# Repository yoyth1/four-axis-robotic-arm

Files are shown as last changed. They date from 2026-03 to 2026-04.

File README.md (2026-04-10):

# Four-Axis Robotic Arm (STM32 + Unity + MATLAB)

本项目为四轴机械臂毕业设计开源仓库，包含机械结构设计、运动学建模验证、硬件电路设计以及 STM32 驱动与上位机联动。

## 项目概览

- 机械结构：基于 SolidWorks 建模，完成底座、腰关节、大臂、小臂与夹爪结构设计。
- 运动学：完成正运动学与逆运动学推导，并用 MATLAB 进行验证。
- 硬件设计：包含控制板/电路相关资料与 PCB 源文件。
- 控制系统：下位机使用 STM32（Keil 工程），上位机使用 Unity 3D。

## 效果与资料预览

### 结构图与样机实物

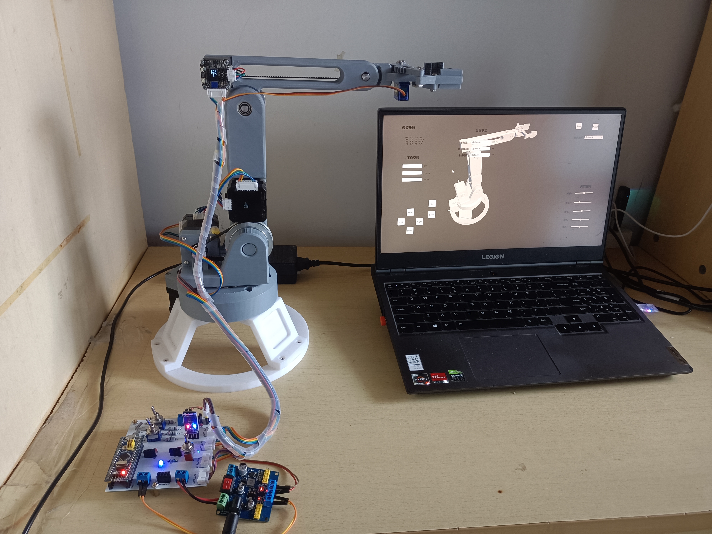
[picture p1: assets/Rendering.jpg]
Rendering

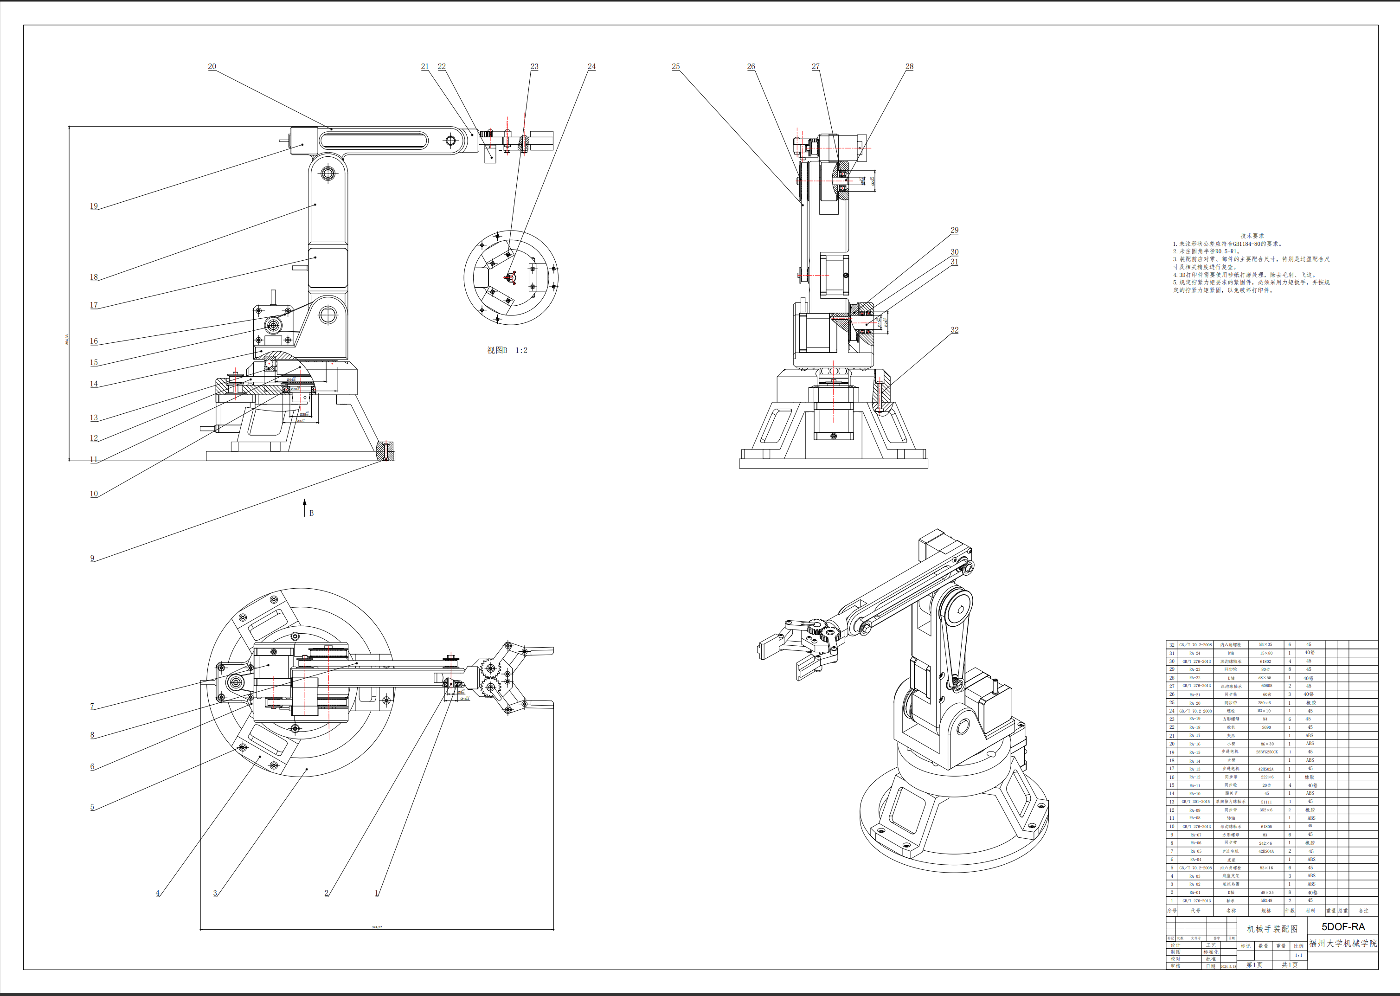
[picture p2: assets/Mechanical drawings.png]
Mechanical drawings.png

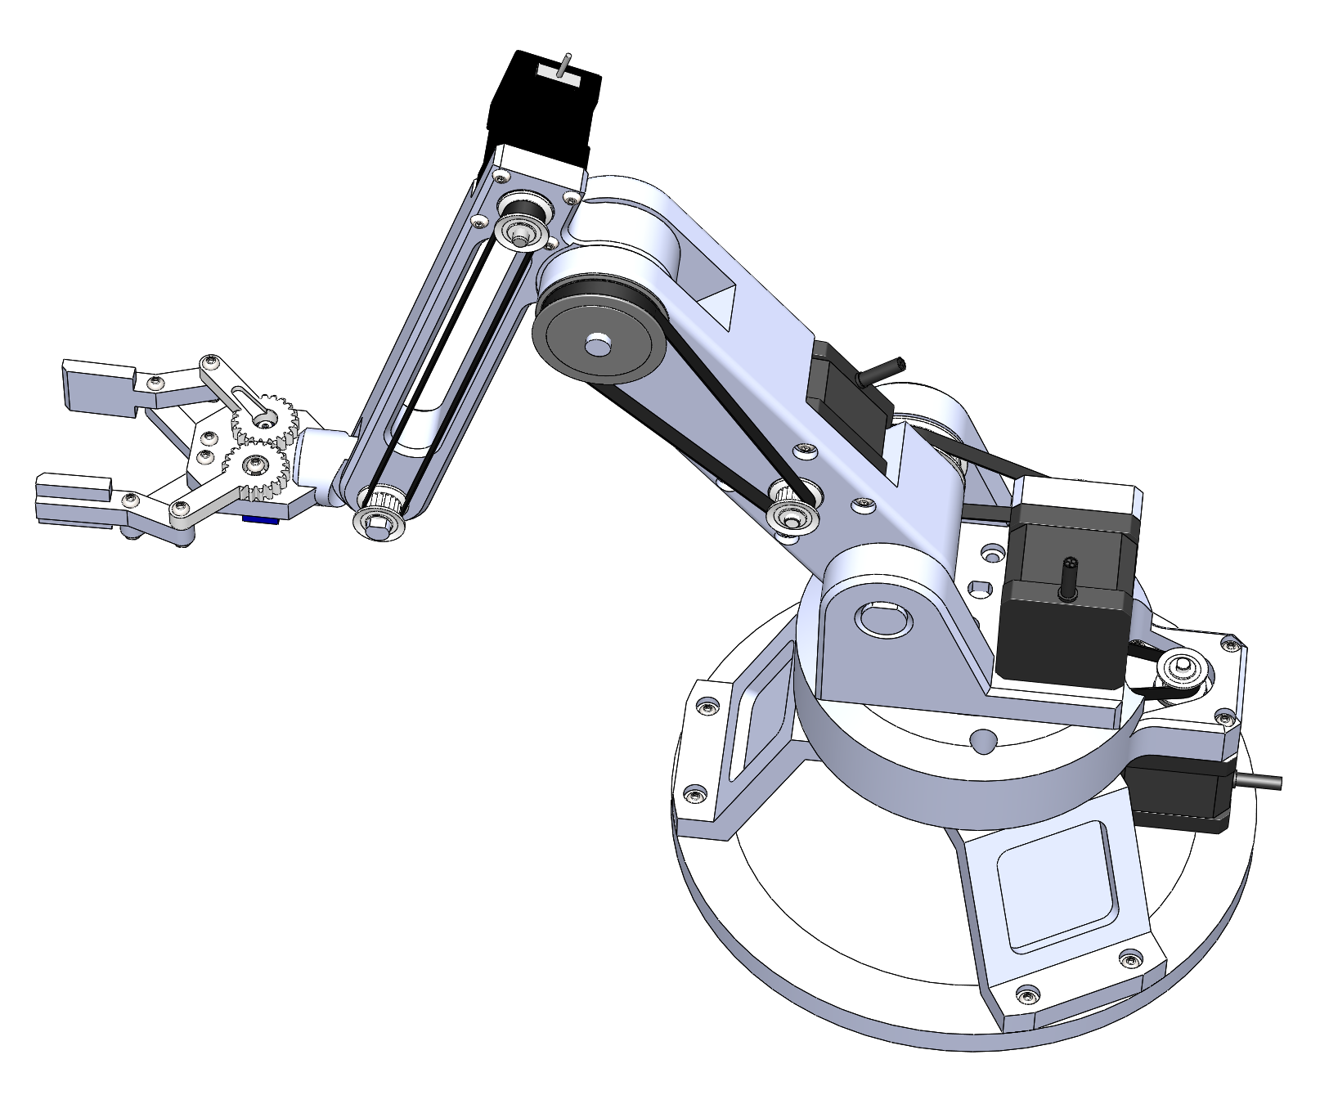
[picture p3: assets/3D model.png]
3D Model


### 系统电路

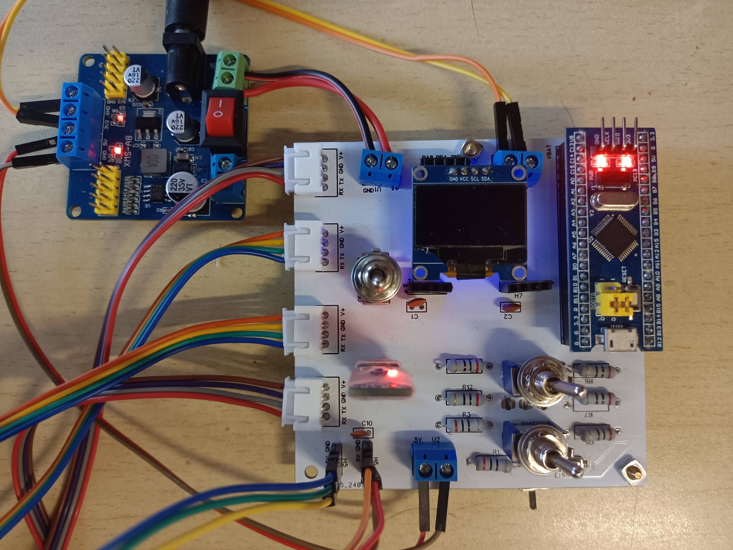
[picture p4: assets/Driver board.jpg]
Driver Board

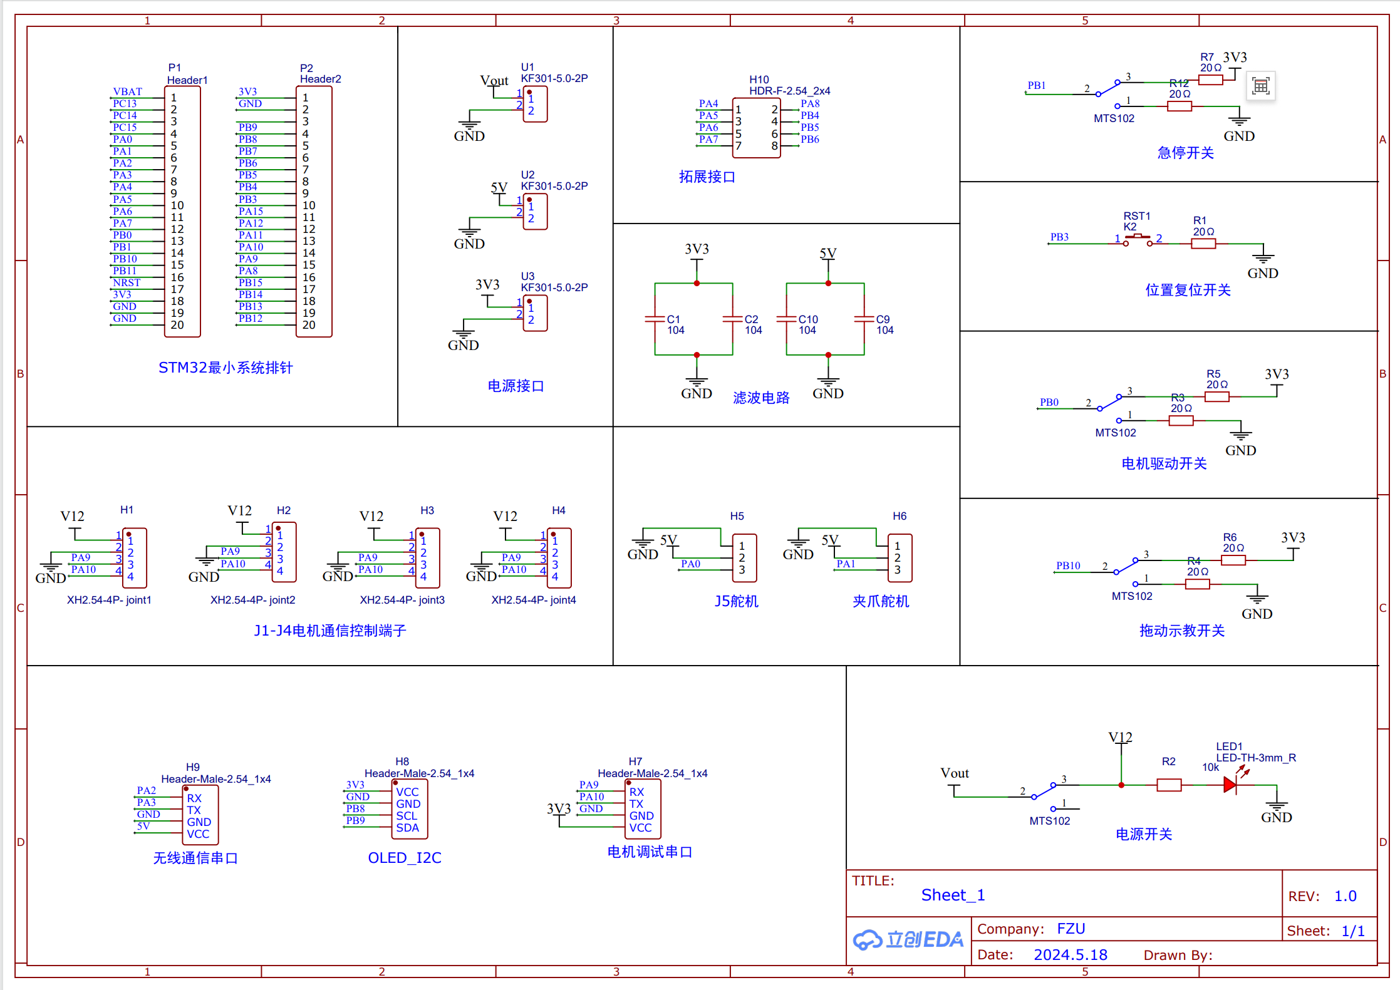
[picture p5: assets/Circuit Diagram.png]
Circuit Diagram


### 上位机界面

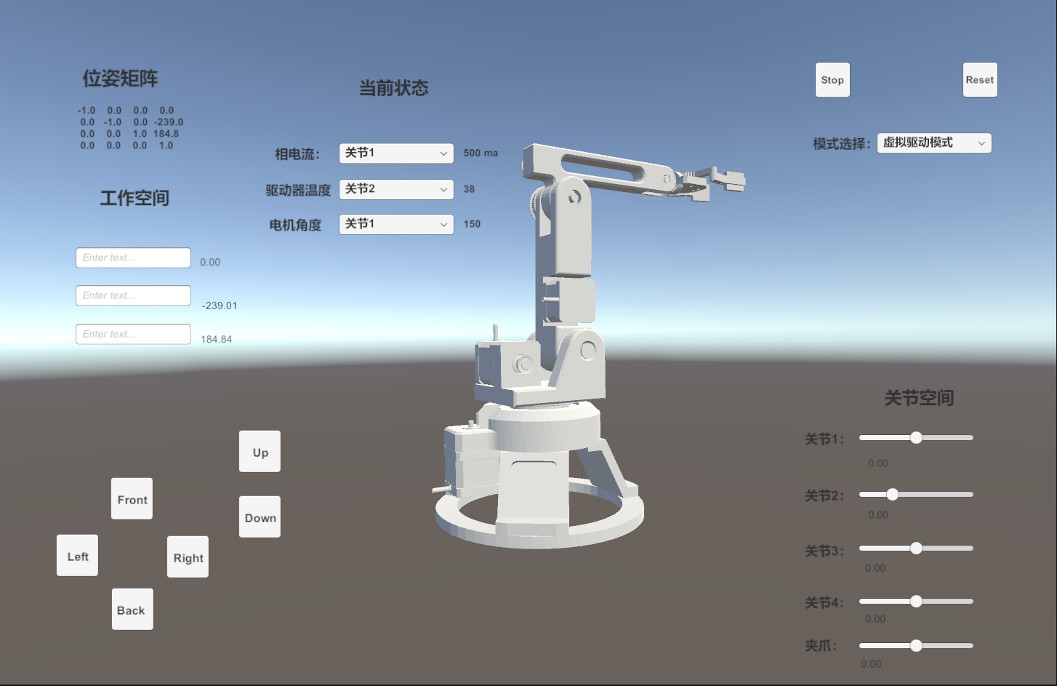
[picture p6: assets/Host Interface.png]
Host Interface


## 仓库结构

| 路径 | 说明 |
|---|---|
| `app/` | Unity 3D 上位机程序（当前仓库为构建产物） |
| `matlab/` | 运动学验证代码（含 D-H 建模与逆解相关脚本） |
| `model/` | 机械臂 3D 模型Solidworks文件 |
| `assets/` | README 图片、电路图、机械图纸等资料 |
| `Stm32_Project/` | STM32 下位机控制代码（Keil 工程） |

## DH 参数与正逆运动学

机械臂采用标准 D-H 建模，共 5 个连杆（4 个主控关节 + 末端夹爪）。MATLAB 验证代码见 `matlab/dh.m` 与 `matlab/inverse_kinematics.m`。

### D-H 参数表

| 连杆 | $\theta$ | $d$ (mm) | $a$ (mm) | $\alpha$ (°) |
|:---:|:---:|:---:|:---:|:---:|
| 0-1 | $-90°+\theta_1$ | 0 | 29 | -90 |
| 1-2 | $-90°+\theta_2$ | 0 | 150 | 0 |
| 2-3 | $75°+\theta_3$ | 0 | 134.5 | 0 |
| 3-4 | $65°+\theta_4$ | 0 | 0 | 90 |
| 4-5 | $-90°+\theta_5$ | 80 | 0 | 90 |

### 正运动学

将各关节 D-H 变换矩阵依次右乘，得到末端相对基座的总变换矩阵：

$$
A_1 =
\begin{bmatrix}
C_1 & 0 & -S_1 & a_1 C_1 \\
S_1 & 0 & C_1 & a_1 S_1 \\
0 & -1 & 0 & 0 \\
0 & 0 & 0 & 1
\end{bmatrix}
$$

$$
A_2 =
\begin{bmatrix}
C_2 & -S_2 & 0 & a_2 C_2 \\
S_2 & C_2 & 0 & a_2 S_2 \\
0 & 0 & 1 & 0 \\
0 & 0 & 0 & 1
\end{bmatrix}
$$

$$
A_3 =
\begin{bmatrix}
C_3 & -S_3 & 0 & a_3 C_3 \\
S_3 & C_3 & 0 & a_3 S_3 \\
0 & 0 & 1 & 0 \\
0 & 0 & 0 & 1
\end{bmatrix}
$$

$$
A_4 =
\begin{bmatrix}
C_4 & 0 & S_4 & 0 \\
S_4 & 0 & -C_4 & 0 \\
0 & 1 & 0 & 0 \\
0 & 0 & 0 & 1
\end{bmatrix}
$$

$$
A_5 =
\begin{bmatrix}
C_5 & 0 & S_5 & 0 \\
S_5 & 0 & -C_5 & 0 \\
0 & 1 & 0 & d_5 \\
0 & 0 & 0 & 1
\end{bmatrix}
$$

总变换矩阵展开式：

$$
{}^0T_H =
\begin{bmatrix}
C_{234}C_1C_5 - S_1S_5 & S_{234}C_1 & C_1 C_{234}S_5 + S_1C_5 & C_1(a_1 + d_5 S_{234} + a_3 C_{23} + a_2 C_2) \\
C_1S_5 + S_{234}S_1C_5 & S_{234}S_1 & S_1 C_{234}S_5 - C_1C_5 & S_1(a_1 + d_5 S_{234} + a_3 C_{23} + a_2 C_2) \\
-S_{234}C_5 & C_{234} & -S_{234}S_5 & d_5 C_{234} + a_3 S_{23} - a_2 S_2 \\
0 & 0 & 0 & 1
\end{bmatrix}
$$

### 逆运动学

为了方便表示，将上面的矩阵表示为 *RHS*（Right-Hand Side）。将机械臂末端的期望位姿表示为：

$$
{}^R T_H =
\begin{bmatrix}
n_x & o_x & a_x & p_x \\
n_y & o_y & a_y & p_y \\
n_z & o_z & a_z & p_z \\
0 & 0 & 0 & 1
\end{bmatrix}
$$

根据期望末端位姿 ${}^RT_H$，采用代数解耦法，依次反解各关节角，求解顺序如下：

**① 求 $\theta_5$**：由总变换矩阵 $(3,2)$ 元素对应关系得

$$
\theta_5 = \arctan\left(\frac{a_z}{n_z}\right)
$$

**② 求 $\theta_1$**：由 $(1,4)$、$(2,4)$ 元素得

$$
\theta_1 = \arctan\left(\frac{p_y - d_5 o_y}{p_x - d_5 o_x}\right)
$$

**③ 求 $\theta_3$**：利用 $\theta_1$ 已知，由 $(2,4)$、$(3,4)$ 建立方程后两边平方相加，利用 $S_2 S_{23} + C_2 C_{23} = C_3$ 化简得

$$
C_3 =
\frac{
\left(d_5 o_z - p_z\right)^2 +
\left(\dfrac{p_y - d_5 o_y}{S_1} - a_1\right)^2 -
a_2^2 - a_3^2
}{
2 a_2 a_3
}
$$

$$
\theta_3 =
\arctan\left(\frac{\pm\sqrt{1-C_3^2}}{C_3}\right)
$$

**④ 求 $\theta_2$**：令 $\tan\phi = \dfrac{a_3 S_3}{a_3 C_3 + a_2}$，则

$$
\theta_2 =
\arcsin\left(
\frac{d_5 o_z - p_z}{\sqrt{a_2^2 + a_3^2 + 2 a_2 a_3 C_3}}
\right) - \phi
$$

**⑤ 求 $\theta_4$**：由 $(3,3)$ 元素 $\cos(\theta_2+\theta_3+\theta_4) = o_z$ 得

$$
\theta_4 = \arccos(o_z) - \theta_2 - \theta_3
$$

## 环境与使用说明

### 1) STM32 下位机

- 工程路径：`Stm32_Project/Project.uvprojx`
- 目标芯片：`STM32F103C8`（Cortex-M3）
- 开发环境：Keil MDK（uVision）
- 使用方式：打开工程、编译后通过 ST-Link 等方式下载到开发板。
- 通过串口与上位机通信

### 2) MATLAB 运动学验证

- 代码路径：`matlab/`
- 主要脚本：`dh.m`、`inverse_kinematics.m`、`dof_5.m`
- 说明：脚本使用机器人运动学工具箱相关能力（如 `SerialLink`），需要配置matlab Robotic Toolbox工具箱。

### 3) Unity 上位机

- 程序路径：`app/`
- 说明：当前仓库目前仅提供上位机构建结果，可直接运行并与下位机联调。
  
### 演示视频
- https://www.bilibili.com/video/BV1QucRzZEsu/?vd_source=743b9fd8168666d94b81cdd6a7604898#reply116205826345706

## 开源说明

### License

 MIT 或其软硬件项目的许可证
### 免责声明

本项目主要用于学习与毕业设计交流。请在实际制作、调试和使用过程中自行评估风险，作者不对由此产生的直接或间接损失负责。

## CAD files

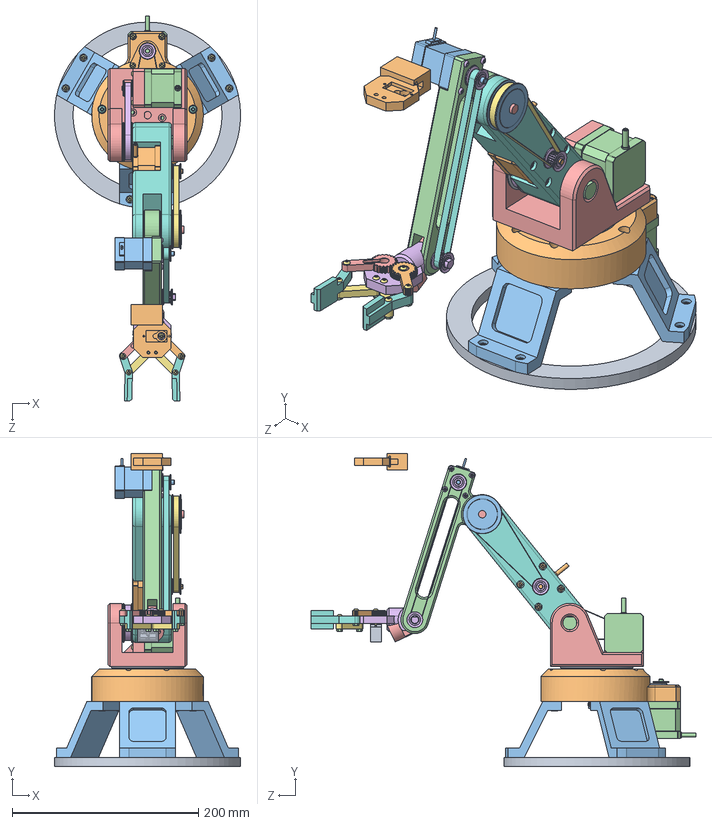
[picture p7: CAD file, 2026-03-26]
model/装配图.SLDASM
199.9 x 336.6 x 413.8 mm
底座环
底座盘
底座支架 x 3
42系列两相混合式步进电机[42HS04A] x 2
关节1
2GT型A形圆孔同步带轮[TPAC20GT2060-A-H4] x 5
GB╱T 276-2013[深沟球轴承[60000]61802] x 4
大臂
2GT型A形圆孔同步带轮[TPAC60GT2060-A-H8]
42系列两相混合式步进电机[42HS02A]
两相28系列混合式步进电机[28BYG250CK-SASSML-0071]
小臂
夹爪架
夹爪臂 x 2
夹爪小爪 x 2
A形树脂直齿轮[SGPOS1-20-10-A-8]
Servo Motor (SG90)(used)
齿轮2
直孔同步带轮 2GT型[60-2GT-6-6F] x 2
D轴15mm
d轴 x 2
D轴8x20
轴承8x14x4 x 2
GB╱T 276-2013[两面带防尘盖的深沟球轴承[60000-2Z]608-2Z] x 2
GB╱T 276-1994[两面带密封圈（接触式）的深沟球轴承[60000-2LS]61805-2LS]
GB╱T 70.2-2015[内六角平圆头螺钉M3×8] x 4
轴
轴盖
hexagon socket button head screws gb x 4
GB╱T 70.2-2015[内六角平圆头螺钉M3×16] x 21
GB╱T 70.2-2015[内六角平圆头螺钉M4×30] x 6
GB╱T 301-2015[单向推力球轴承[51000型]51111]
GB╱T 39-1988[方螺母 C级M3] x 6
GB╱T 39-1988[方螺母 C级M4] x 6
GB╱T 6170-2000[1型六角螺母 A级和B级M3] x 6
GB╱T 70.2-2008[内六角平圆头螺钉M3×10] x 3
同步带2^底座
同步带3^底座
零件3^底座
同步带1^底座

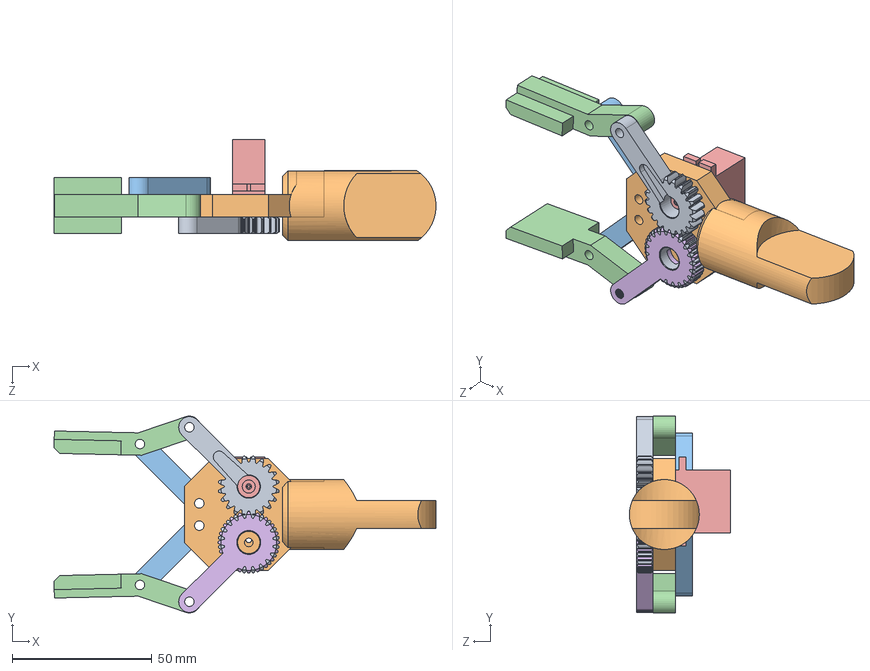
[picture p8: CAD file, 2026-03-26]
model/夹爪.SLDASM
136.6 x 70.4 x 36.2 mm
夹爪架
夹爪臂 x 2
夹爪小爪 x 2
A形树脂直齿轮[SGPOS1-20-10-A-8]
Servo Motor (SG90)(used)
齿轮2

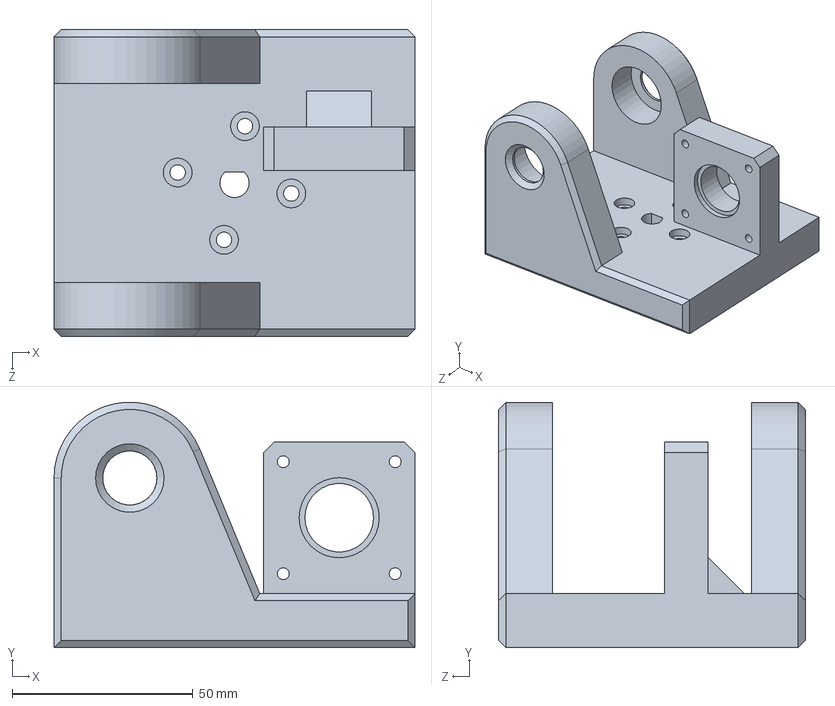
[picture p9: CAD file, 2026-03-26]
model/关节1.SLDPRT
100.0 x 68.0 x 85.0 mm

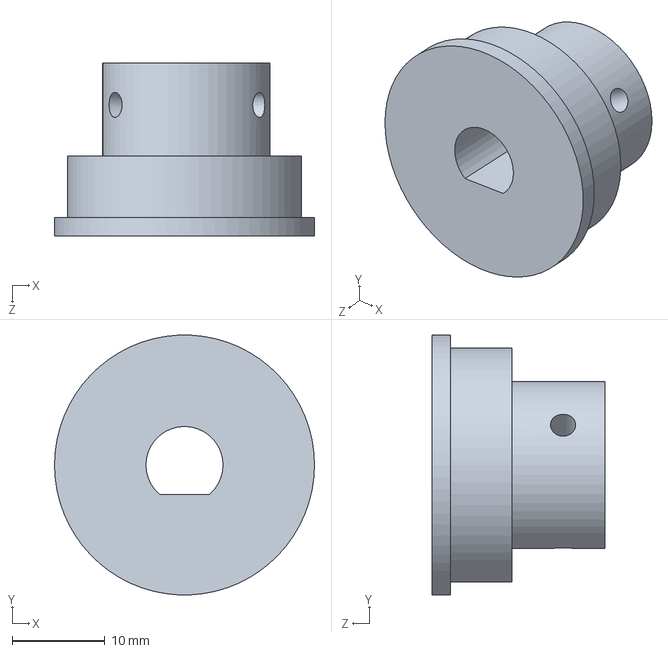
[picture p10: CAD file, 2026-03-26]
model/轴.SLDPRT
28.0 x 28.0 x 18.6 mm

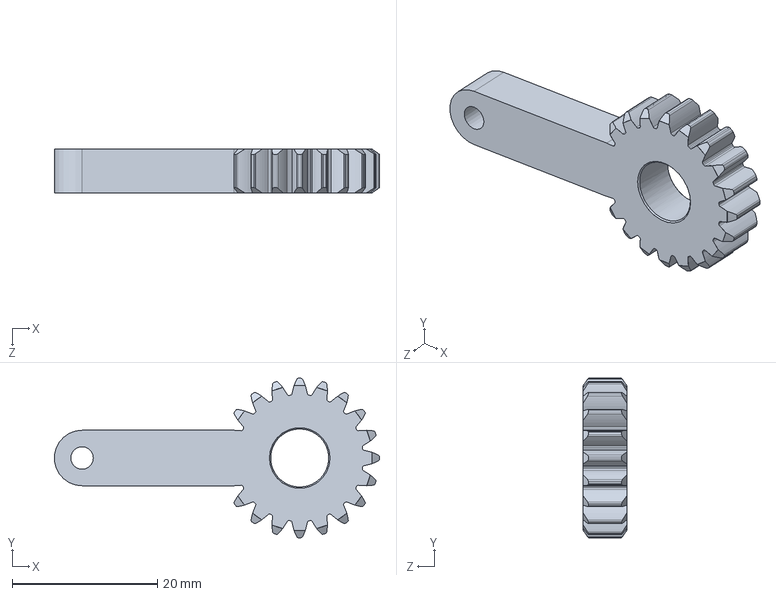
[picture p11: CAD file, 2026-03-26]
model/A形树脂直齿轮[SGPOS1-20-10-A-8].sldprt
44.8 x 22.0 x 6.00 mm

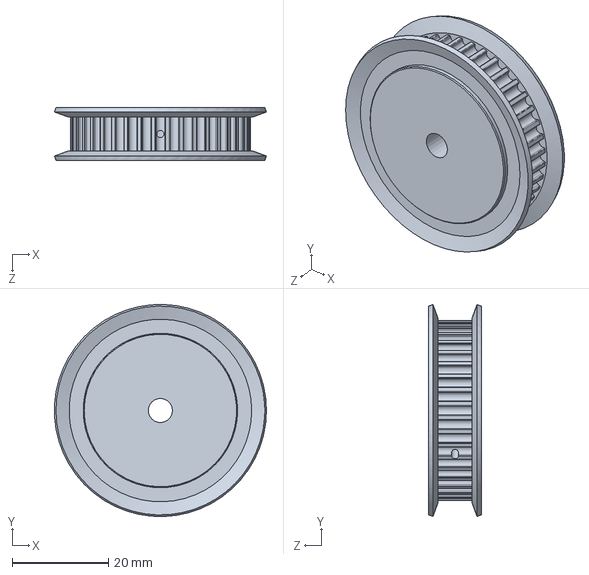
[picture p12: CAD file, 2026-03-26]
model/标准型圆弧型齿HTD3M-A同步轮支持定制[SLA40-3M060-A-P10].sldprt
44.0 x 44.0 x 11.0 mm

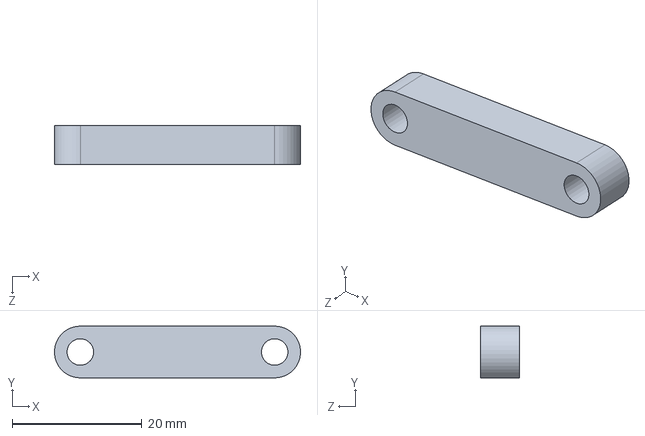
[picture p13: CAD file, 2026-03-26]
model/夹爪臂.SLDPRT
38.0 x 8.00 x 6.00 mm

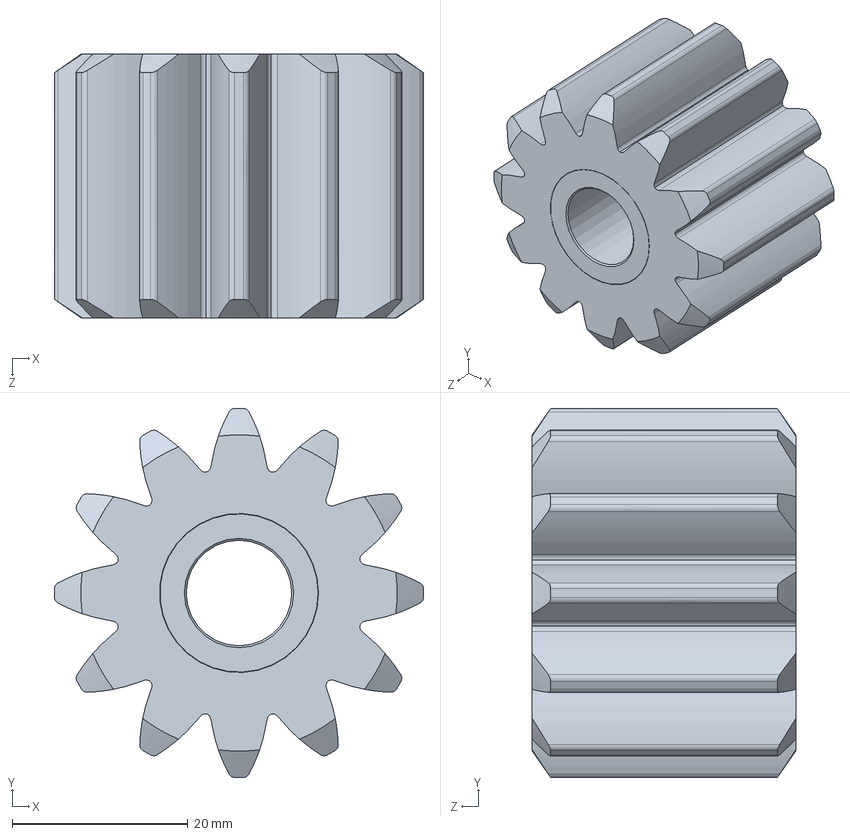
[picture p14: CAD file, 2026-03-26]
model/A形树脂直齿轮[SGMC3-12-30-A-12].sldprt
42.0 x 42.0 x 30.0 mm

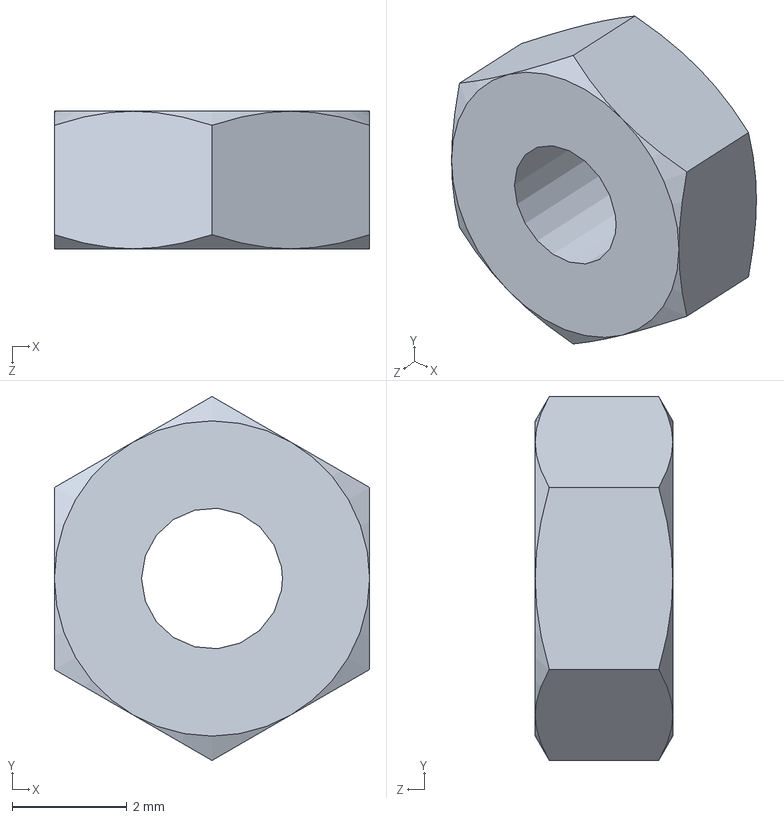
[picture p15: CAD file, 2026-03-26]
model/GB╱T 6170-2000[1型六角螺母 A级和B级M3].sldprt
5.50 x 6.35 x 2.40 mm

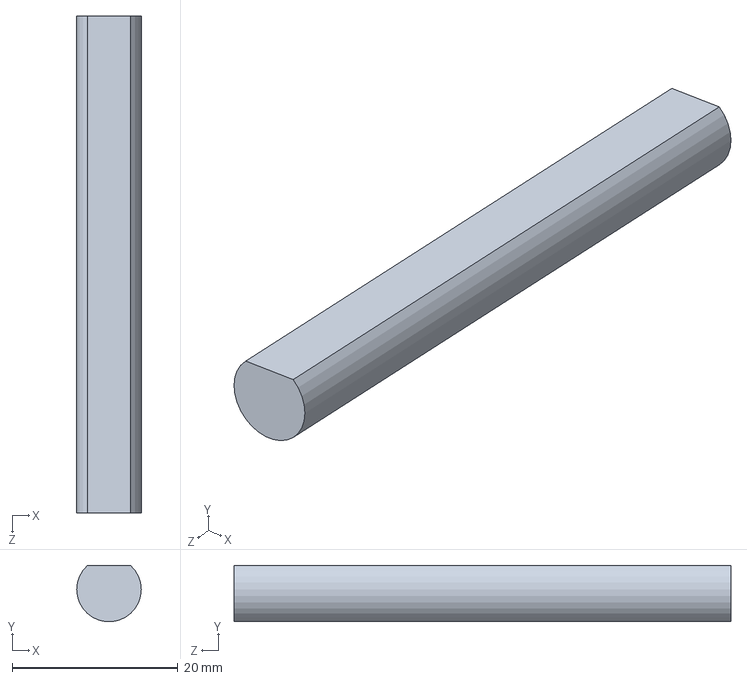
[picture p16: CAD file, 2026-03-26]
model/D轴8x20.SLDPRT
7.80 x 6.78 x 60.0 mm

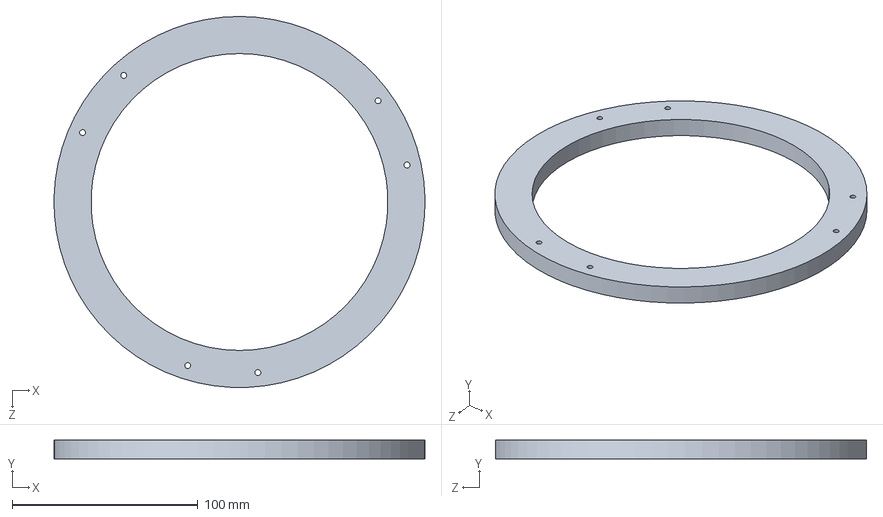
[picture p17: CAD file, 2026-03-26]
model/底座环.SLDPRT
199.9 x 10.0 x 200.0 mm

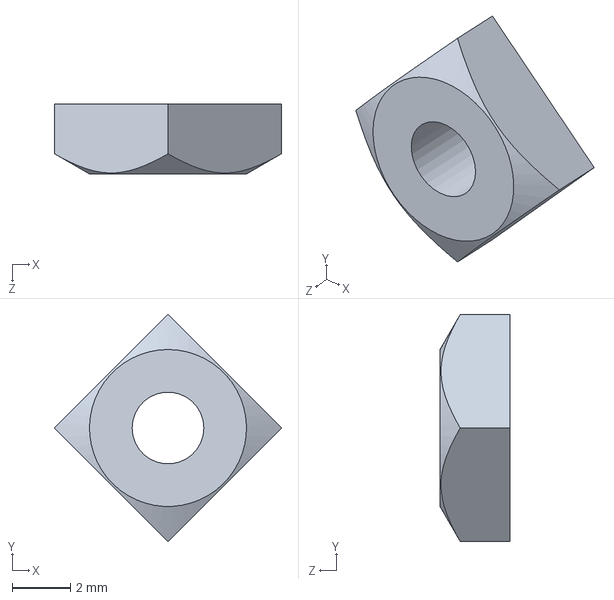
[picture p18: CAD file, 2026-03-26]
model/GB╱T 39-1988[方螺母 C级M3].sldprt
7.78 x 7.78 x 2.40 mm

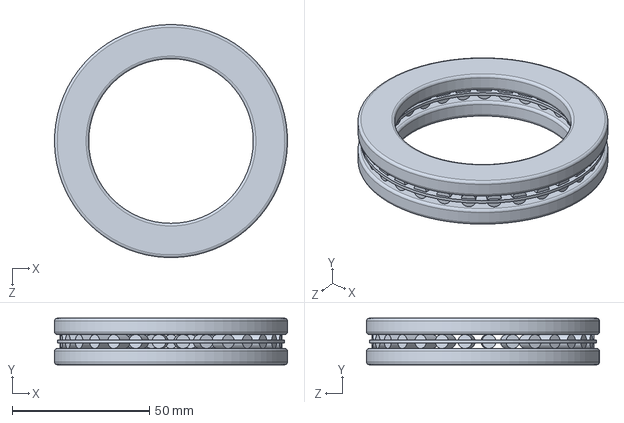
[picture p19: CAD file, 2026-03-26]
model/GB╱T 4663-2017[单向推力圆柱滚子轴承81112 GB╱T 4663-2017].sldprt
85.0 x 17.0 x 85.0 mm

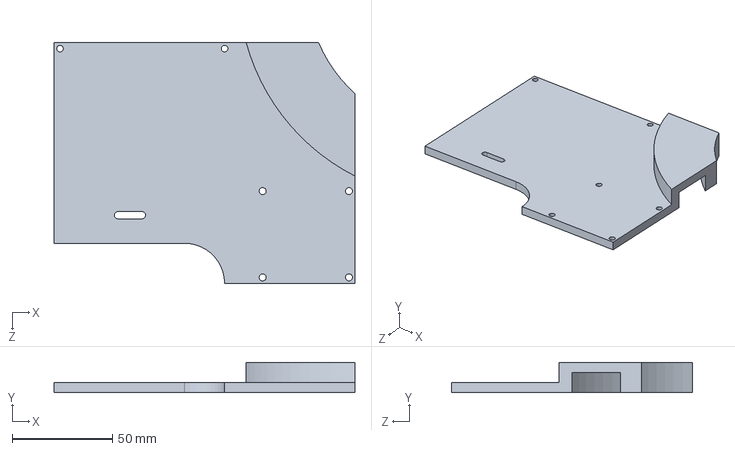
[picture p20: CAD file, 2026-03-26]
model/电路板支架.SLDPRT
150.0 x 15.0 x 120.0 mm

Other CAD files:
model/GB╱T 70.2-2015[内六角平圆头螺钉M3×8].sldprt
model/底座支架.SLDPRT
model/两相28系列混合式步进电机[28BYG250CK-SASSML-0071].SLDPRT
model/底座盘.SLDPRT
model/2GT型A形圆孔同步带轮[TPAC20GT2060-A-H4].sldprt
model/2GT型A形圆孔同步带轮[TPAC60GT2060-A-H8].sldprt
model/42系列两相混合式步进电机[42HS02A].sldprt
model/42系列两相混合式步进电机[42HS04A].sldprt
model/42系列两相混合式步进电机[42HS07A].sldprt
model/A形树脂直齿轮[SGMC3-14-30-A-12].sldprt
model/A形树脂直齿轮[SGPOS1.5-15-15-A-8].sldprt
model/A形树脂直齿轮[SGPOS2-14-20-A-10].sldprt
model/D轴15mm.SLDPRT
model/GB╱T 276-1994[两面带密封圈（接触式）的深沟球轴承[60000-2LS]61805-2LS].sldprt
model/GB╱T 276-2013[两面带防尘盖的深沟球轴承[60000-2Z]608-2Z].sldprt
model/GB╱T 276-2013[深沟球轴承[60000]61802].sldprt
model/GB╱T 301-2015[单向推力球轴承[51000型]51111].sldprt
model/GB╱T 39-1988[方螺母 C级M4].sldprt
model/GB╱T 4663-1994[推力圆柱滚子轴承[80000]81108].sldprt
model/GB╱T 4663-2017[单向推力圆柱滚子轴承81111 GB╱T 4663-2017].sldprt
model/GB╱T 70.2-2008[内六角平圆头螺钉M3×10].sldprt
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

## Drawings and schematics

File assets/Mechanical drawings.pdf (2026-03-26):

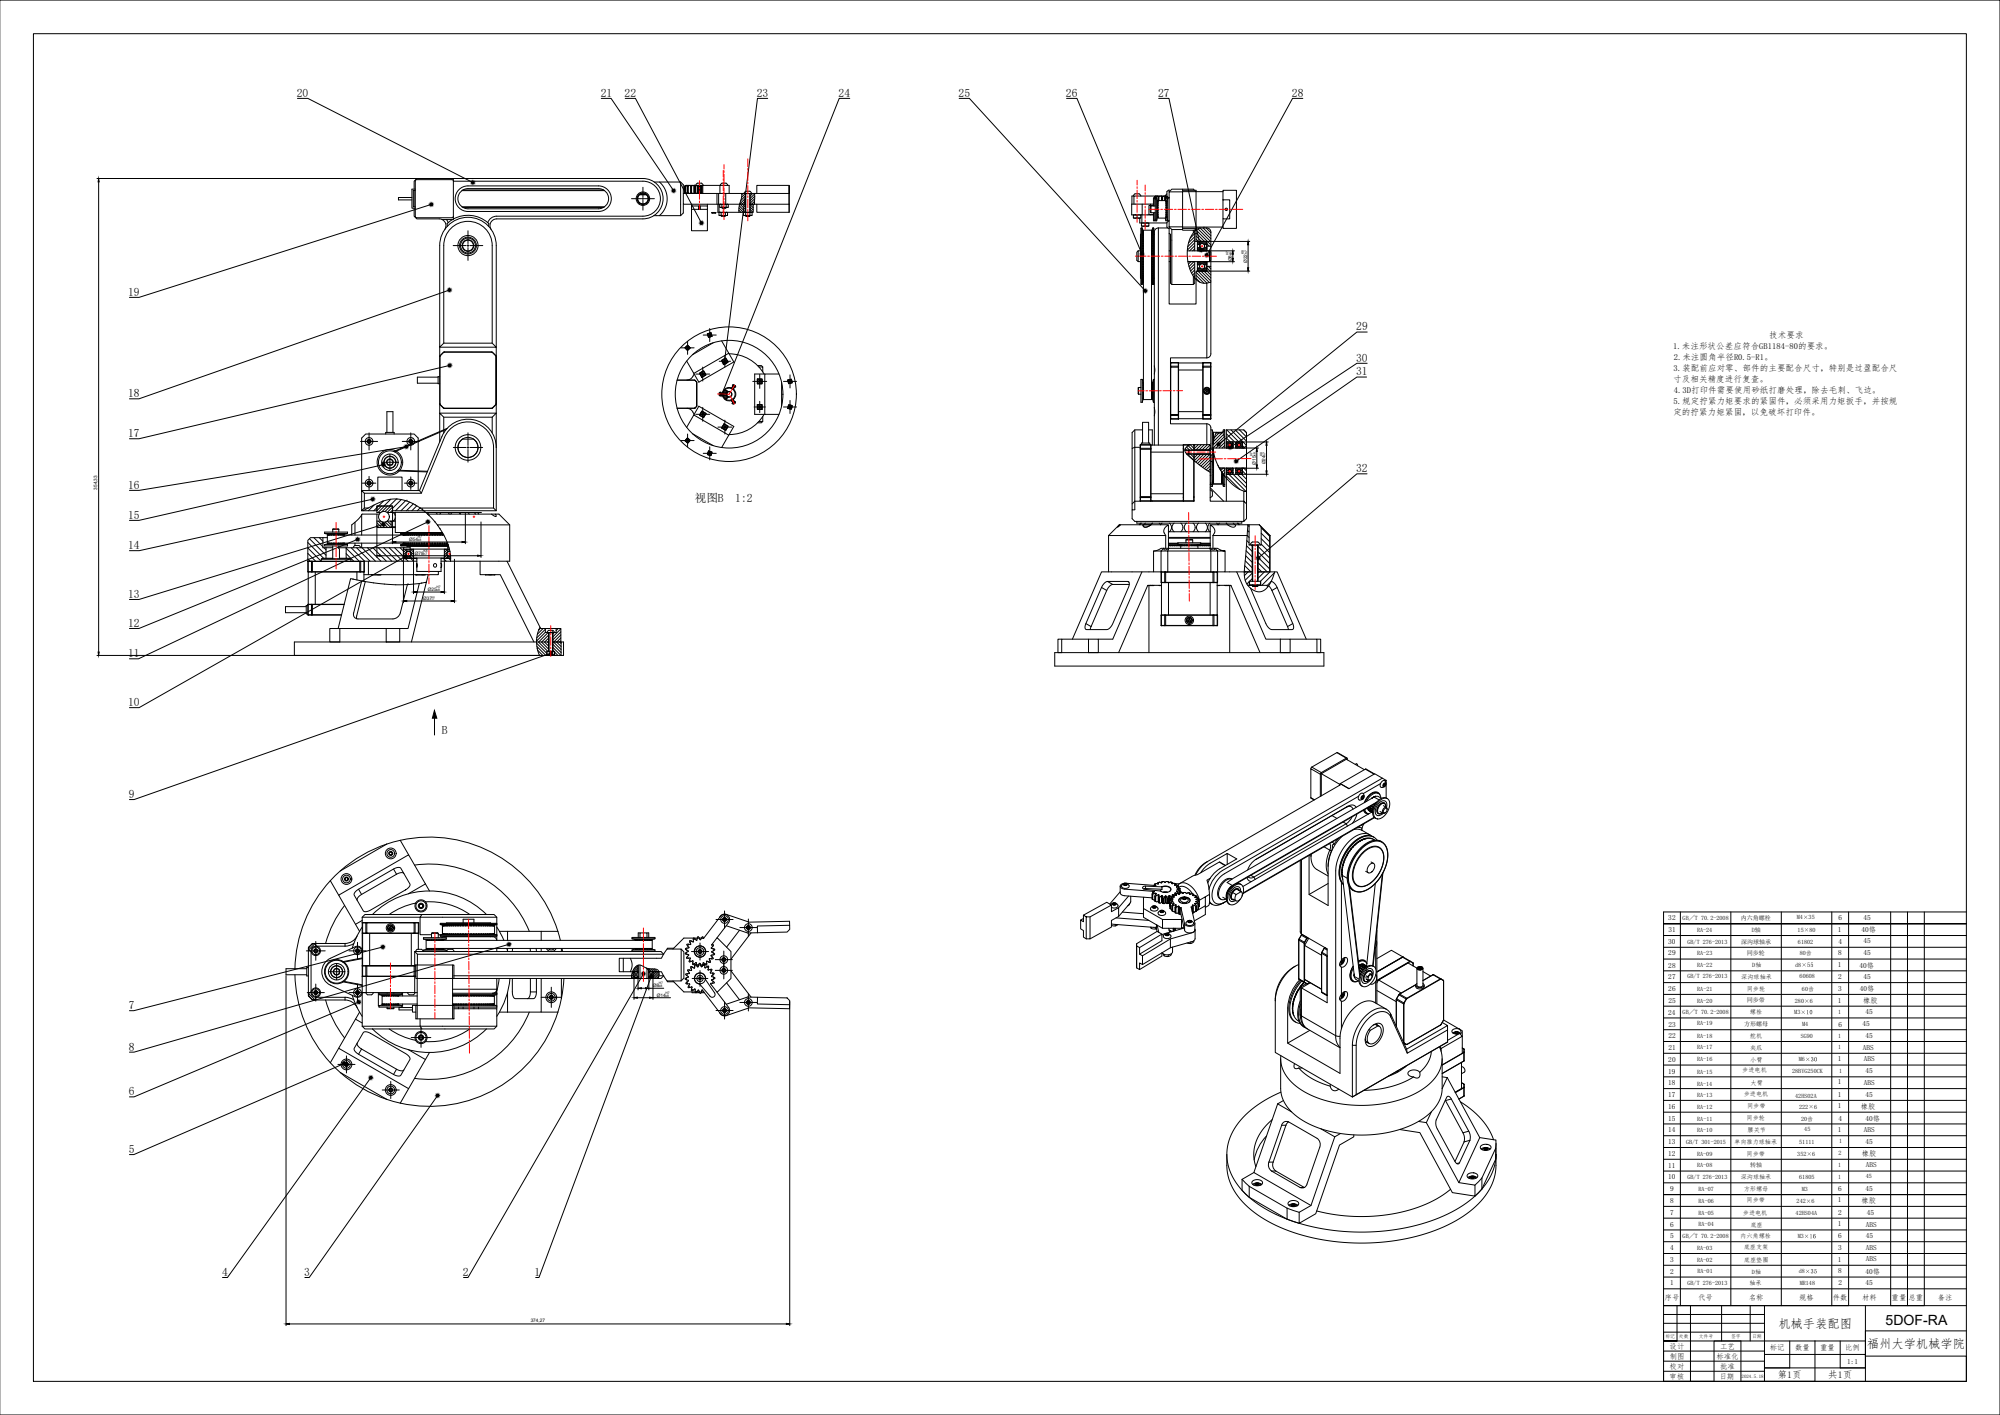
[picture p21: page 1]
标准化 序号; 文件号; 日期 校对 标记设计; 重量 总重 机械手装配图; 福州大学机械学院 ABS 8; ABS 40铬 6; ABS 16 D轴轴承; 5DOF-RA RA-01; 底座垫圈 底座支架 内六角螺栓 RA-04; 底座 同步带 方形螺母; 1 同步带 7; 腰关节; 2 深沟球轴承; ABS 2 45; 45 ABS 同步轮; 40铬 1 同步带; 1 步进电机; ABS 步进电机; ABS 舵机; 45 方形螺母; 45 同步轮; 3 同步带; 橡胶 深沟球轴承; 1 同步轮; 45 深沟球轴承; ABS 2024.5.18 4; MR148 42HS04A 242×6 单向推力球轴承 步进电机; 橡胶橡胶 42HS02A 28BYG250CK M3M4 M3×10 280×6 GB/T 276-2013 GB/T 276-2013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

354,33 374,27 31 32 内六角螺栓 M4×35 6 45 15×80 GB╱T 70.2-2008 视图B 1:2 80齿 B 橡胶 GB/T 276-2013 GB╱T 70.2-2008 GB/T 276-2013 RA-02 RA-03 RA-08 RA-09 RA-10 RA-11 RA-12 RA-13 RA-14 RA-15 RA-16 RA-17 RA-18 GB╱T 70.2-2008 RA-20 RA-21 RA-22 RA-23 RA-24 d8×55 RA-19 40铬 40铬40铬 Ø25H7 k8 Ø37K8h7 Ø78K8h7 Ø54H7 k8

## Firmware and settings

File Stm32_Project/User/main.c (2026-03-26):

#include "stm32f10x.h"   // Device header
#include "Delay.h"
#include "OLED.h"
#include "Serial.h"
#include "Key.h"
#include "usart.h"
#include "Servo.h"
#include "Timer.h"
uint8_t KeyNum;
int main(void)
{
	OLED_Init();    //OLED显示屏初始化
	Key_Init();     //按键初始化
	Serial_Init();	//无线串口模块初始化          
    Timer_Init();	//定时器初始化
	Servo_Init();	//舵机模块初始化
	board_init();	//电机通信初始化
	Delay_ms(2000);	//等待去电机驱动初始化完成
	
	while (1)		//显示屏循环显示数据
	{
	 
		OLED_ShowArry(1, Serial_RxPacket, 12); //显示无线串口数据
		OLED_ShowNum(1, 12, KeyNum,4);
		KeyNum+=1;
				
	}
	
	
}





//			OLED_ShowHexNum(4, 1, Serial_TxPacket[0], 2);
//			OLED_ShowHexNum(4, 4, Serial_TxPacket[1], 2);
//			OLED_ShowHexNum(4, 7, Serial_TxPacket[2], 2);

//			OLED_ShowHexNum(1, 1, Serial_RxPacket[0], 2);
//			OLED_ShowHexNum(1, 4, Serial_RxPacket[1], 2);
//			OLED_ShowHexNum(1, 7, Serial_RxPacket[2], 2);
//			OLED_ShowHexNum(1, 1, Serial_RxPacket[3], 2);;
	

     //uint8_t KeyNum;
	//	KeyNum+=1;

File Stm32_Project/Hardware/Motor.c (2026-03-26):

#include "stm32f10x.h"                  // Device header
#include "Motor.h"
#include <math.h>
#include "Emm_V5.h"
#include "Serial.h"
#include "OLED.h"
#include "Delay.h"
#include "Servo.h"
void SetStepMotor(u8 *Arry)   //解析关节角度值并发送给电机驱动
{
	int16_t Angles[6];
	for(u8 i=0;i<6;i++)
	{
		Angles[i]=((int16_t)Arry[2*i])<<8;
		Angles[i]|=(int16_t)Arry[2*i+1]; 
	}
	Emm_V5_Pos_Control(1, (Angles[0]>=0)? 1:0, MoterSpeed, MoterAcc, abs((int)(Angles[0]*0.78125))*4, 1, 0);//设置第一关节角度   4为减速比
	Delay_ms(10);
	Emm_V5_Pos_Control(2, (Angles[1]>=0)? 1:0, MoterSpeed, MoterAcc, abs((int)(Angles[1]*0.78125))*4, 1, 0);//设置第二关节角度
	Delay_ms(10);
	Emm_V5_Pos_Control(3, (Angles[2]>=0)? 1:0, MoterSpeed, MoterAcc, abs((int)(Angles[2]*0.78125))*3, 1, 0);
	Delay_ms(10);
	Emm_V5_Pos_Control(4, (Angles[3]>=0)? 1:0, MoterSpeed, MoterAcc, abs((int)(Angles[3]*0.78125))*1, 1, 0);
	Delay_ms(10);
	Servo1_SetAngle((float)((180.0*Angles[5]/32768.0)+90));   //设置关节五舵机角度
	Servo_SetAngle((float)((180.0*Angles[5]/32768.0)+90));    //设置夹爪舵机角度
		
	//设置舵机和四五关节
}


void USART2_IRQHandler(void)  //接收到数据后对数据进行解析
{
	static uint8_t RxState = 0;
	static uint8_t pRxPacket = 0;
	if (USART_GetITStatus(USART2, USART_IT_RXNE) == SET)
	{
		uint8_t RxData = USART_ReceiveData(USART2);
		
		if (RxState == 0)
		{
			if (RxData == 0xA5)
			{
				RxState = 1;
				pRxPacket = 0;
			}
		}
		else if (RxState == 1)
		{
			Serial_RxPacket[pRxPacket] = RxData;
			pRxPacket ++;
			if (pRxPacket >= 12)
			{
				RxState = 2;
			}
		}
		else if (RxState == 2)
		{
			if (RxData == 0x66)
			{
				RxState = 0;
				Serial_RxFlag = 1;		
				SetStepMotor(Serial_RxPacket);
			}
		}	
		USART_ClearITPendingBit(USART2, USART_IT_RXNE);
			
	}
}



void EXTI1_IRQHandler(void)  //外部中断函数，按下实现急停
{
	if (EXTI_GetITStatus(EXTI_Line1) == SET)
	{
		int i=100;
		while(i!=0)              //延时  消抖
			i--;
 
		
		
		
		
		
      if (GPIO_ReadInputDataBit(GPIOB, GPIO_Pin_1) == 0)
	{
//		OLED_ShowString(4, 1, "Start");
//		TIM_Cmd(TIM3, ENABLE);
//		Emm_V5_En_Control(0,0, 0);   //失能电机驱动
		Serial_SendByte(0xA5);	    
		Serial_SendByte(0x23);       //发送开始示教指令
		Serial_SendByte(0x66);

	}
	
	
	
	else if (GPIO_ReadInputDataBit(GPIOB, GPIO_Pin_0) == 1)
		{
//			TIM_Cmd(TIM3, DISABLE);
//			Emm_V5_En_Control(0,1, 0);
//			OLED_ShowString(4, 1, "End");	
			Serial_SendByte(0xA5);	
			Serial_SendByte(0x24);	//发送停止示教指令
			Serial_SendByte(0x66);
		}	

		
		
		
		
		

		EXTI_ClearITPendingBit(EXTI_Line1);   

	}
}



void TIM3_IRQHandler(void)  //外部中断函数，按下实现实物驱动
{
	if (TIM_GetITStatus(TIM3, TIM_IT_Update) == SET)
	{
				
			for(u8 i=0;i<4;i++)
			{
               __IO uint16_t t0 = 0;  

				Emm_V5_Read_Sys_Params(i+1,S_CPOS); // 读取参数
				
				while(rxFrameFlag==false)        //接收到一帧数据					
				{
					++t0; if(t0 > 3000)	{	break; }
				}
					
				if(rxFrameFlag)
				{
					Serial_TxPacket[4*i] =rxCmd[2];
					Serial_TxPacket[4*i+1] =rxCmd[4]; //地址 + 0x37 + 符号 + 电机位置+ 校验字节  01 表示负数(00 表示正数)，00 01 00 00 表示电机实时位置值
					Serial_TxPacket[4*i+2] =rxCmd[5];
					Serial_TxPacket[4*i+3] =rxCmd[6];

				}
				rxFrameFlag=false;
			}

				Serial_SendPacket();
			    TIM_ClearITPendingBit(TIM3, TIM_IT_Update);
			
	}
}


void EXTI0_IRQHandler(void)  //外部中断 实现按键按下开始拖动示教
{
	if (EXTI_GetITStatus(EXTI_Line0) == SET)
	{
		int i=100;
		while(i!=0)              //延时  消抖
			i--;

		if (GPIO_ReadInputDataBit(GPIOB, GPIO_Pin_0) == 0)
	{
		OLED_ShowString(4, 1, "Physical Drive");
		TIM_Cmd(TIM3, ENABLE);
		Emm_V5_En_Control(0,0, 0);   //失能电机驱动
//		Serial_SendByte(0xA5);	    
//		Serial_SendByte(0x23);       //发送开始示教指令
//		Serial_SendByte(0x66);

	}
	
	
	
	else if (GPIO_ReadInputDataBit(GPIOB, GPIO_Pin_0) == 1)
		{
			TIM_Cmd(TIM3, DISABLE);
			Emm_V5_En_Control(0,1, 0);
			OLED_ShowString(4, 1, "Virtual Drive");	
//			Serial_SendByte(0xA5);	
//			Serial_SendByte(0x24);	//发送停止示教指令
//			Serial_SendByte(0x66);
		}	

		EXTI_ClearITPendingBit(EXTI_Line0);   

	}
	
}



void EXTI15_10_IRQHandler(void)  //急停
{
	OLED_ShowString(4, 1, "End");
	if (EXTI_GetITStatus(EXTI_Line10) == SET)
	{
		int i=100;
		while(i!=0)              //延时消抖
			i--;

	//	//	如果出现数据乱跳的现象，再次判断引脚电平，以避免抖动
		if (GPIO_ReadInputDataBit(GPIOB, GPIO_Pin_1) == 0)
	{
		Emm_V5_Stop_Now(0, 0); // 让电机立即停止运动
		//Emm_V5_En_Control(0,0,0);  //失能电机
	}
	   else  if (GPIO_ReadInputDataBit(GPIOB, GPIO_Pin_1) == 1)
	{
		Emm_V5_Stop_Now(0, 0); // 让电机立即停止运动
		//Emm_V5_En_Control(0,0,0);  //失能电机
	}
		
		
		
		
    }
	EXTI_ClearITPendingBit(EXTI_Line10);   

	
}

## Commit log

2026-03-26 Initial commit: open-source four-axis robotic arm project
    Prepare the repository for GitHub publication with documentation, assets, firmware, models, and MATLAB verification scripts.
    Made-with: Cursor
    [2GT型A形圆孔同步带轮[TPAC20GT2060-A-H4].sldprt, 2GT型A形圆孔同步带轮[TPAC60GT2060-A-H8].sldprt, 42系列两相混合式步进电机[42HS02A].sldprt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]
2026-03-26 Refine kinematic equations in README
    Updated equations and notation for kinematic transformations.
2026-04-10 补充图纸
